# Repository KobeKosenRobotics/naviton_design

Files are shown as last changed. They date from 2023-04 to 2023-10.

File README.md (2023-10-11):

# naviton_design
[Naviton](https://github.com/KobeKosenRobotics/naviton)'s cad data and electric circuits



## Supporting format
### [Hardware design](https://github.com/KobeKosenRobotics/naviton_design/tree/main/hardware_design)
* Autodesk Inventor (.iam .ipt)
* Step file (.stp)
### [Electric design](https://github.com/KobeKosenRobotics/naviton_design/tree/main/electric_design)
* Autodesk Eagle(.brd .sch)

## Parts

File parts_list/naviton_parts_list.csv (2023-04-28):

カテゴリ | iam | メモ、備考 | 優先度 | 商社 | メーカー | メーカー型番 | 商社品名 | 注文コード | 数量 | 単価 | 小計
機械 | 機体 |  |  |  | amazon |  | ステンレス蝶番 ドアヒンジ 4‘’x3‘’ 厚さ3mm平蝶番 折り畳みヒンジ ドア用金物 家具補修 ステンレス鋼ねじ付き シルバー （2個セット ） | https://www.amazon.co.jp/%E3%82%B9%E3%83%86%E3%83%B3%E3%83%AC%E3%82%B9%E8%9D%B6%E7%95%AA-4%E2%80%98%E2%80%99x3%E2%80%98%E2%80%99-%E5%8E%9A%E3%81%953mm%E5%B9%B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 | 1
機械 | 機体 |  |  |  | amazon | 銅カットワイヤと100均箱で代用 | アスベル 保存容器 「Agタイトロック」 TLO-20 ナチュラル | https://www.amazon.co.jp/%E3%82%A2%E3%82%B9%E3%83%99%E3%83%AB-%E4%BF%9D%E5%AD%98%E5%AE%B9%E5%99%A8-%E3%80%8CAg%E3%82%BF%E3%82%A4%E3%83%88%E3%83%AD%E3%83%83%E3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 | 2
機械 | 機体 |  |  |  | amazon | 60Kg二軸サーボ 教育娯楽ロボットサーボ スマートロボットサーボ (180°) | 60Kg二軸サーボ 教育娯楽ロボットサーボ スマートロボットサーボ (180°) | https://www.amazon.co.jp/%E3%82%BE%E3%83%BC%E3%82%B9%E3%82%AB%E3%82%A4-60Kg%E4%BA%8C%E8%BB%B8%E3%82%B5%E3%83%BC%E3%83%9C-%E6%95%99%E8%82%B2%E5%A8%AF%E6%A5%BD%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 | 2
機械 | フレーム |  |  | 1 | misumi | HFS5-2020-800 | 高剛性フレーム | https://jp.misumi-ec.com/vona2/detail/110302683830/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 | 4
機械 | フレーム |  |  | 1 | misumi | HFS5-2020-300 | 高剛性フレーム | https://jp.misumi-ec.com/vona2/detail/110302683830/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 | 2
機械 | フレーム |  |  | 1 | misumi | HFS5-2020-716 | 高剛性フレーム | https://jp.misumi-ec.com/vona2/detail/110302683830/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 | 2
機械 | フレーム |  |  | 1 | misumi | HFS5-2020-500 | 高剛性フレーム | https://jp.misumi-ec.com/vona2/detail/110302683830/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 | 2
機械 | フレーム |  |  | 1 | misumi | HFS5-2020-600 | 高剛性フレーム | https://jp.misumi-ec.com/vona2/detail/110302683830/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 | 2
機械 | フレーム |  |  | 1 | misumi | HFS5-2020-400 | 高剛性フレーム | https://jp.misumi-ec.com/vona2/detail/110302683830/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 | 10
機械 | フレーム |  |  | 1 | misumi | HBLFSN5-SEP | ブラケット2 | https://jp.misumi-ec.com/vona2/detail/110300437260/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 | 54
機械 | フレーム |  |  | 1 | misumi | HFS5-2020-230 | 高剛性フレーム | https://jp.misumi-ec.com/vona2/detail/110302683830/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 | 2
機械 | フレーム |  |  | 1 | misumi | HFS5-2020-150 | 高剛性フレーム | https://jp.misumi-ec.com/vona2/detail/110302683830/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 | 2
機械 | 車軸部分 |  |  | 1 | misumi | SSFRHP12-140-F10-P8 | 車軸 | https://jp.misumi-ec.com/vona2/detail/110300088140/?HissuCode=SSFRHP12-140-F10-P8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 | 2
機械 | 車軸部分 |  |  | 1 | misumi | 自作or外注 カーボン化検討 | 車輪ハブ1 |  | 2
機械 | 車軸部分 |  |  | 1 | misumi | C-SFL6901ZZ | ベアリング12x18 | https://jp.misumi-ec.com/vona2/detail/110302554510/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 | 4
機械 | 車軸部分 |  |  | 1 | misumi | MJT-30C-RD-8-12 | カップリング | https://jp.misumi-ec.com/vona2/detail/221000131358/?KWSearch=MJT-30&searchFlow=results2products | 2
機械 | 車軸部分 |  |  | 1 | misumi | SCS12-12 | セットカラー | https://jp.misumi-ec.com/vona2/detail/110302636410/ | 4
機械 | 車軸部分 |  |  | 1 | misumi | 外注 | 車軸受け板3 | https://drive.google.com/file/d/1rCQuDQpkBceSkfm0FtveReuvyQ9fZlK2/view?usp=sharing | 4
機械 | 車軸部分 |  |  | 1 | misumi | SAPL-A-12X26 | メカロック | https://jp.misumi-ec.com/vona2/detail/221005492544/ | 2
機械 | 機体 |  |  | 1 | misumi | 477 | クッション | https://jp.misumi-ec.com/vona2/detail/223006733714/?searchFlow=results2products&list=PageSearchResult | 8
機械 |  |  |  | 1 | misumi | 外注 材質(SPCC(SPHC))表面処理(塗装(近似マンセル値2.5Y8/14)) | 緊急停止スイッチマウント |  | 2
機械 | 機体 |  |  |  | misumi | 外注(PET(スタンダード・透明)) | 防水1 |  | 2
機械 | 機体 |  |  |  | misumi | 外注(PET(スタンダード・透明)) | 防水2 |  | 1
機械 | 機体 |  |  |  | misumi | 外注(PET(スタンダード・透明)) | 防水4 |  | 1
機械 | 機体 |  |  |  | misumi | 外注(PET(スタンダード・透明)) | 防水3 |  | 1
機械 | 自由輪 |  |  | 3 | monotaro | ナンシン プレート式 自在、ゴム(B入り)車 車輪径D 150Φmm、許容荷重 160daN、STC-150CBC | 自由輪 | https://www.monotaro.com/p/3519/5946/ | 1
機械 | 車軸部分 |  |  | 1 | yahoo | モンキー・ゴリラ用 ８インチ アルミホイール・タイヤセット（ホイール選択：2.5J，タイヤ選択：90/65-8，オプション：組付けなし） | 車輪 | https://store.shopping.yahoo.co.jp/redmotoparts/ca085.html | 2
機械 | 車軸部分 |  |  | 1 | yahoo | 朱雀技研工房 | 小型DCギヤードモータ RS-775GM144-METAL-D Dカット軸・初段金属ギヤ仕様 | https://store.shopping.yahoo.co.jp/suzakulab/rs-775gm144-metal-d.html | 2
機械 | 車軸部分 |  |  |  | yahoo | 朱雀技研工房 | RS-775 1/144 接着剤601 | https://store.shopping.yahoo.co.jp/suzakulab/rs-775gm144-metal-r.html?sc_i=shp_pc_search_itemlist_shsrg_title | 2
機械 | 自由輪 | 外注 |  |  | ニワカソフト | 自由輪治具（t=3mm，d=180mm，w=100mm） | 自由輪マウント |  | 1
機械 | 車軸部分 | 外注 |  |  | ニワカソフト | 外注 カーボン化(t5) | 車軸受け板 |  | 4
機械 | 車軸部分 | 外注 |  |  | ニワカソフト | 外注 カーボン化(t3) | 車軸受け板2 |  | 2
機械 | 機体 | 外注 |  |  | ニワカソフト | 外注 カーボン化(t3) | LRFマウント |  | 2
機械 | 機体 | 教員対応 |  |  | 北陽電機 | UST-30LX | LiDAR |  | 2
機械 | 車軸部分 |  |  |  |  | 3Dプリンタ | モータースペーサ2 |  | 2
機械 | 車軸部分 |  |  |  |  | 3Dプリンタ | モータースペーサ |  | 2
機械 | 車軸部分 |  |  |  |  | 3Dプリンタ | エンコーダガード2 |  | 2
機械 | 機体 | 自作 |  |  |  |  | 回路スペース |  | 1
機械 | 機体 | 自作 |  |  |  |  | 回路スペース2 |  | 1
機械 | 機体 | 自作 |  |  |  |  | タイヤカバー |  | 2
電気部品 | 車軸部分 |  |  | 1 | Marutsu | AMT102-V | AMT102-1 | https://www.marutsu.co.jp/pc/i/1320459/ | 2
電気部品 |  | LANハブ |  | 1 | amazon |  | BUFFALO Giga対応 プラスチック筐体 AC電源 5ポート LSW6-GT-5EPL/NBK ブラック スイッチングハブ ローコストモデル 簡易パッケージ 壁掛け設置対応 日本メーカー | https://www.amazon.co.jp/%E3%83%97%E3%83%A9%E3%82%B9%E3%83%81%E3%83%83%E3%82%AF%E7%AD%90%E4%BD%93-LSW6-GT-5EPL-NBK-%E3%82%B9%E3%82%A4%E3%83%83%E3%83%81%E3%83%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 | 1 | 1280 | 1280
電気部品 |  | usbハブ |  | 1 | amazon |  | Anker USB3.0 ウルトラスリム 4ポートハブ, USB ハブ バスパワー 軽量 コンパクト MacBook / iMac / Surface Pro 等 ノートPC 他対応 USBハブ テレワーク リモート 在宅勤務 | https://www.amazon.co.jp/Anker-USB3-0-%E3%82%A6%E3%83%AB%E3%83%88%E3%83%A9%E3%82%B9%E3%83%AA%E3%83%A0-4%E3%83%9D%E3%83%BC%E3%83%88%E3%83%8F%E3%83%96-%E3%80%90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 | 1 | 1399 | 1399
電気部品 |  | usb延長 |  | 1 | amazon | 右L型 | 変換名人 USB3.0 延長ケーブル 20cm [ Aオス端子・、右L型 ] USB3A-CA20RL | https://www.amazon.co.jp/%E5%A4%89%E6%8F%9B%E5%90%8D%E4%BA%BA-USB3-0-%E5%BB%B6%E9%95%B7%E3%82%B1%E3%83%BC%E3%83%96%E3%83%AB-A%E3%82%AA%E3%82%B9%E7%AB%AF%E5%AD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 | 1 | 575 | 575
電気部品 |  | btドングル |  | 1 | amazon |  | BUFFALO Bluetooth4.0 Class1対応 USBアダプター BSBT4D105BK | https://www.amazon.co.jp/BUFFALO-Bluetooth4-0-Class1%E5%AF%BE%E5%BF%9C-USB%E3%82%A2%E3%83%80%E3%83%97%E3%82%BF%E3%83%BC-BSBT4D105BK/dp/B07716SP6N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 | 1 | 2299 | 2299
電気部品 |  | コントローラ |  | 1 | amazon |  | ワイヤレスコントローラー (DUALSHOCK 4) マグマ・レッド (CUH-ZCT2J11) | https://www.amazon.co.jp/%E3%83%AF%E3%82%A4%E3%83%A4%E3%83%AC%E3%82%B9%E3%82%B3%E3%83%B3%E3%83%88%E3%83%AD%E3%83%BC%E3%83%A9%E3%83%BC-DUALSHOCK-4-%E3%83%9E%E3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 | 1 | 6480 | 6480
電気部品 |  | pro mini |  | 1 | amazon |  | HiLetgo ATMEGA328P 3.3V/8M Arduino PROミニ 互換性のある開発ボード改良版 (3.3V) (2個セット) | https://www.amazon.co.jp/HiLetgo-ATMEGA328P-Arduino-PRO%E3%83%9F%E3%83%8B-%E4%BA%92%E6%8F%9B%E6%80%A7%E3%81%AE%E3%81%82%E3%82%8B%E9%96%8B%E7%99%BA%E3%83%9C%E3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 | 1 | 1030 | 1030
電気部品 |  | mini usb host |  | 1 | amazon |  | GAOHOU ミニUSBホストシールド2.0 ADK SLR開発ツール互換SPIインターフェイス | https://www.amazon.co.jp/GAOHOU-BU0295-%E3%83%9F%E3%83%8BUSB%E3%83%9B%E3%82%B9%E3%83%88%E3%82%B7%E3%83%BC%E3%83%AB%E3%83%892-0-ADK-SLR%E9%96%8B%E7%99%BA%E3%83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 | 1 | 998 | 998
電気部品 |  | 緊急停止スイッチ |  | 1 | misumi | AR30V0R-11R | φ30 非常停止用押しボタンスイッチ AR30形 (AR30V0R-11R) | https://jp.misumi-ec.com/vona2/detail/222000260284/?HissuCode=AR30V0R-11R | 2 | 1289 | 2578
電気部品 |  | モータドライバ |  | 1 | yahoo | 朱雀技研工房 | Cytron 30A 5V-30V DCモータドライバ | https://store.shopping.yahoo.co.jp/suzakulab/cytron-md30c.html# | 2 | 3947 | 7894
電気部品 |  | teensy3.6 |  | 1 | スイッチサイエンス |  | Teensy 3.6 | https://www.switch-science.com/catalog/2989/ | 1 | 4533 | 4533
電気部品 |  | imu |  | 1 | スイッチサイエンス |  | Adafruit BNO055搭載 9DoF 方位/慣性計測モジュール | https://www.switch-science.com/catalog/5511/ | 1 | 5489 | 5489
電気部品 |  | スイッチング電源 |  | 1 | 秋月電子 |  | 最大２Ａ ３～１６Ｖ降圧型スイッチングモジュールキット（ＭＰＭ８０使用） | https://akizukidenshi.com/catalog/g/gK-08572/ | 2 | 750 | 1500

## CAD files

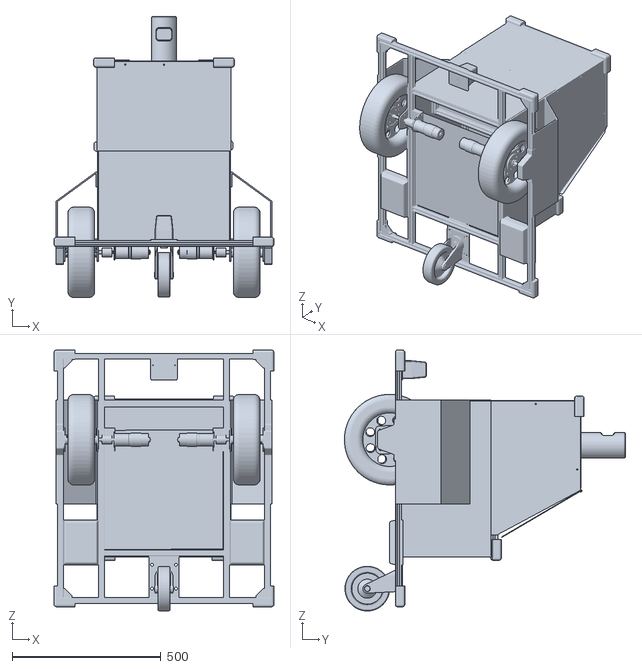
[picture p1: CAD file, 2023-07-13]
hardware_design/naviton.stl
738.0 x 943.7 x 876.0

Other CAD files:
hardware_design/step/機体.stp
hardware_design/inventor/AMT102 outside.ipt
hardware_design/inventor/AMT102-1.ipt
hardware_design/inventor/IG42C-144.ipt
hardware_design/inventor/LRFマウント.ipt
hardware_design/inventor/PCパーツ1.ipt
hardware_design/inventor/PCパーツ2.ipt
hardware_design/inventor/RS-775.ipt
hardware_design/inventor/RS-775GM.ipt
hardware_design/inventor/hdl32e.ipt
hardware_design/inventor/moldspace.iam
hardware_design/inventor/pixy.ipt
hardware_design/inventor/pixymount1.ipt
hardware_design/inventor/pixymount2.ipt
hardware_design/inventor/pixyユニット.iam
hardware_design/inventor/raida- .ipt
hardware_design/inventor/おもり.ipt
hardware_design/inventor/くさび.ipt
hardware_design/inventor/エンコーダガード.ipt
hardware_design/inventor/エンコーダガード2.ipt
hardware_design/inventor/カップリング.ipt
hardware_design/inventor/カメラマウント.ipt
hardware_design/inventor/ガイド輪.ipt
hardware_design/inventor/ガイド輪マウント.ipt
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

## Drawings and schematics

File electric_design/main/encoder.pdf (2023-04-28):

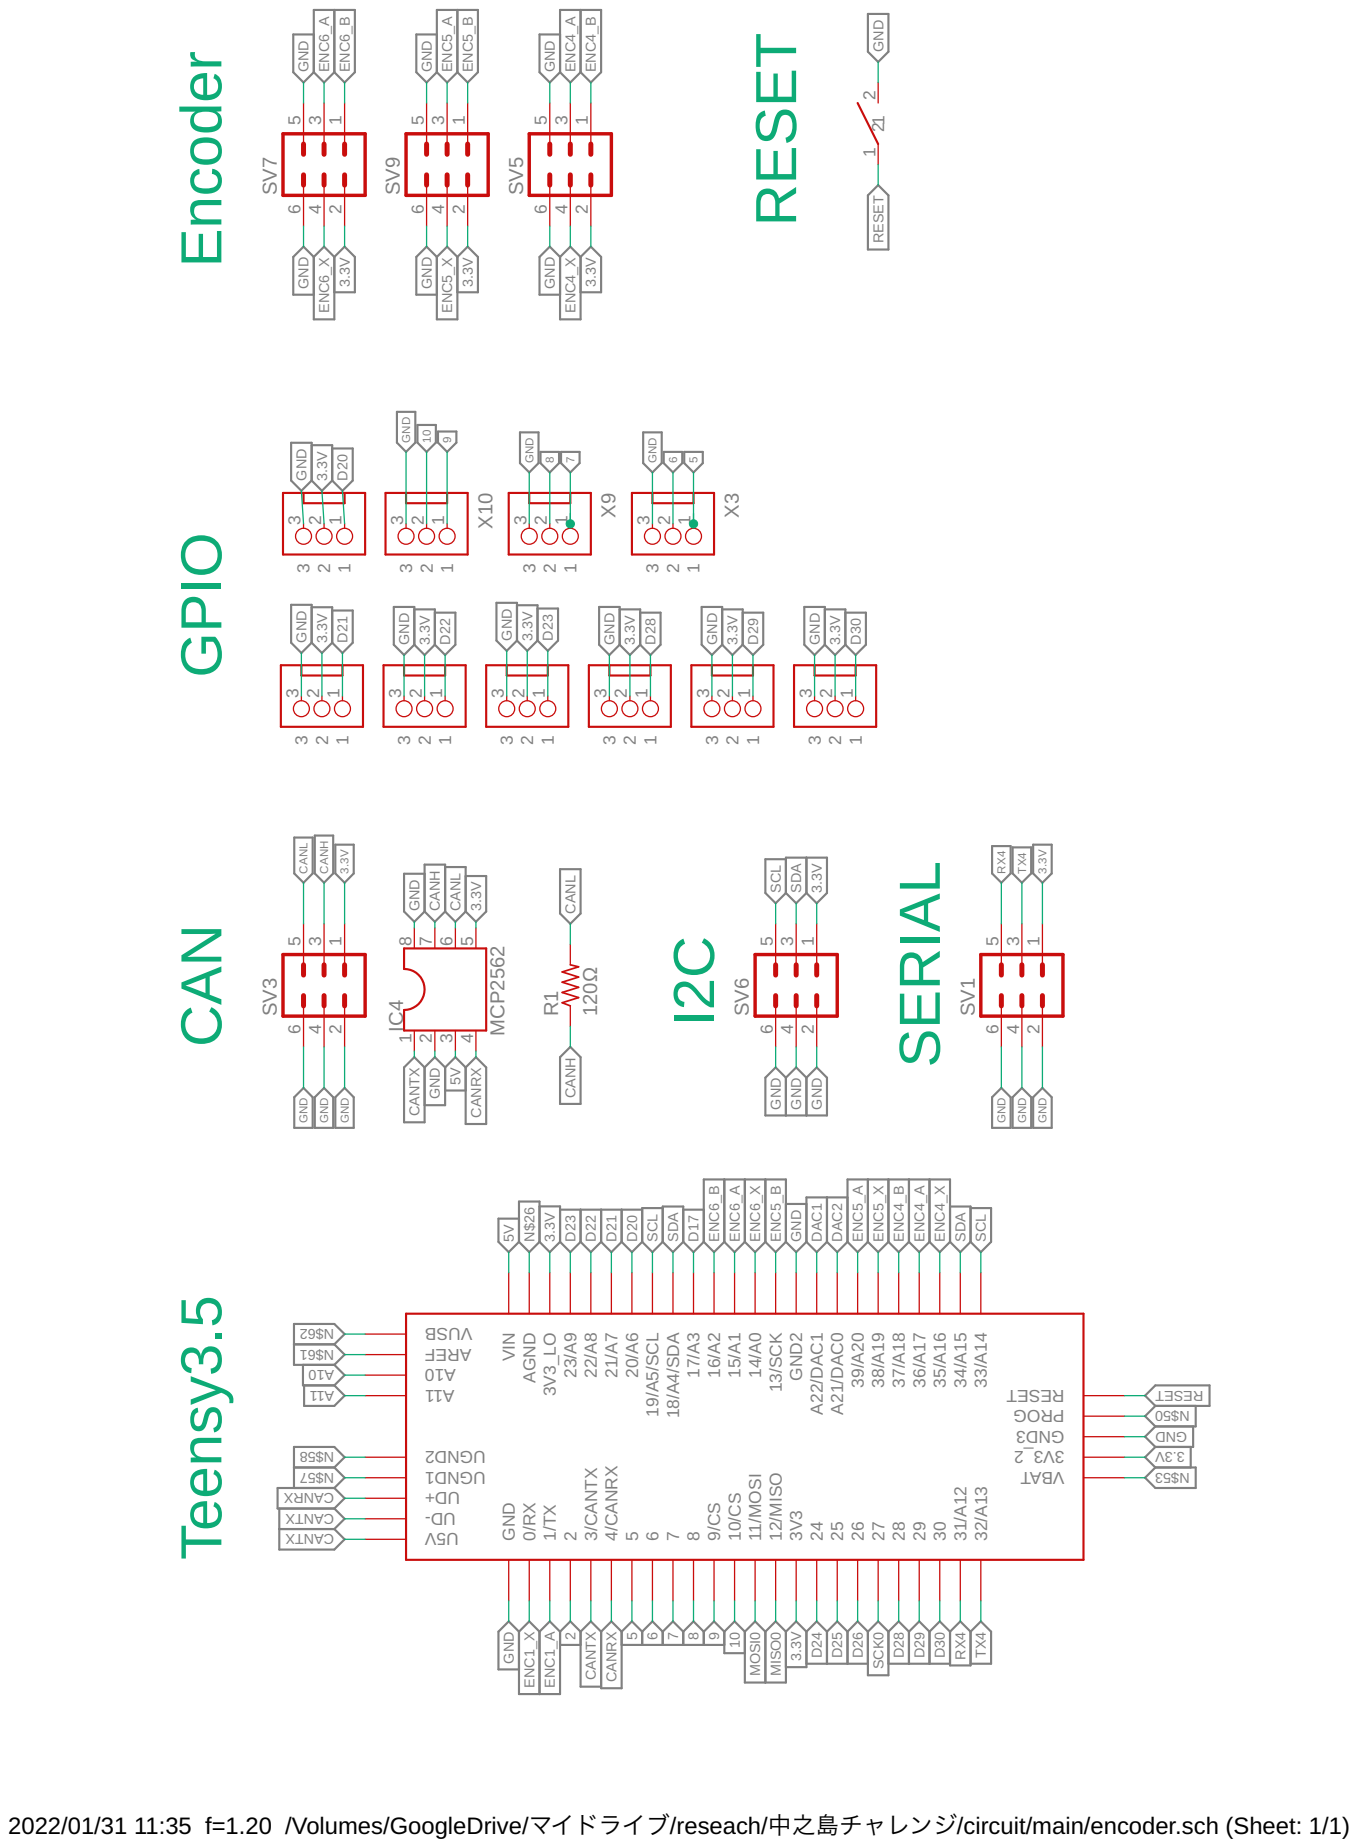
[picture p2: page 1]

GND GND GND GND GND GND GND

2022/01/31 11:35 f=1.20 /Volumes/GoogleDrive/マイドライブ/reseach/中之島チャレンジ/circuit/main/encoder.sch (Sheet: 1/1)

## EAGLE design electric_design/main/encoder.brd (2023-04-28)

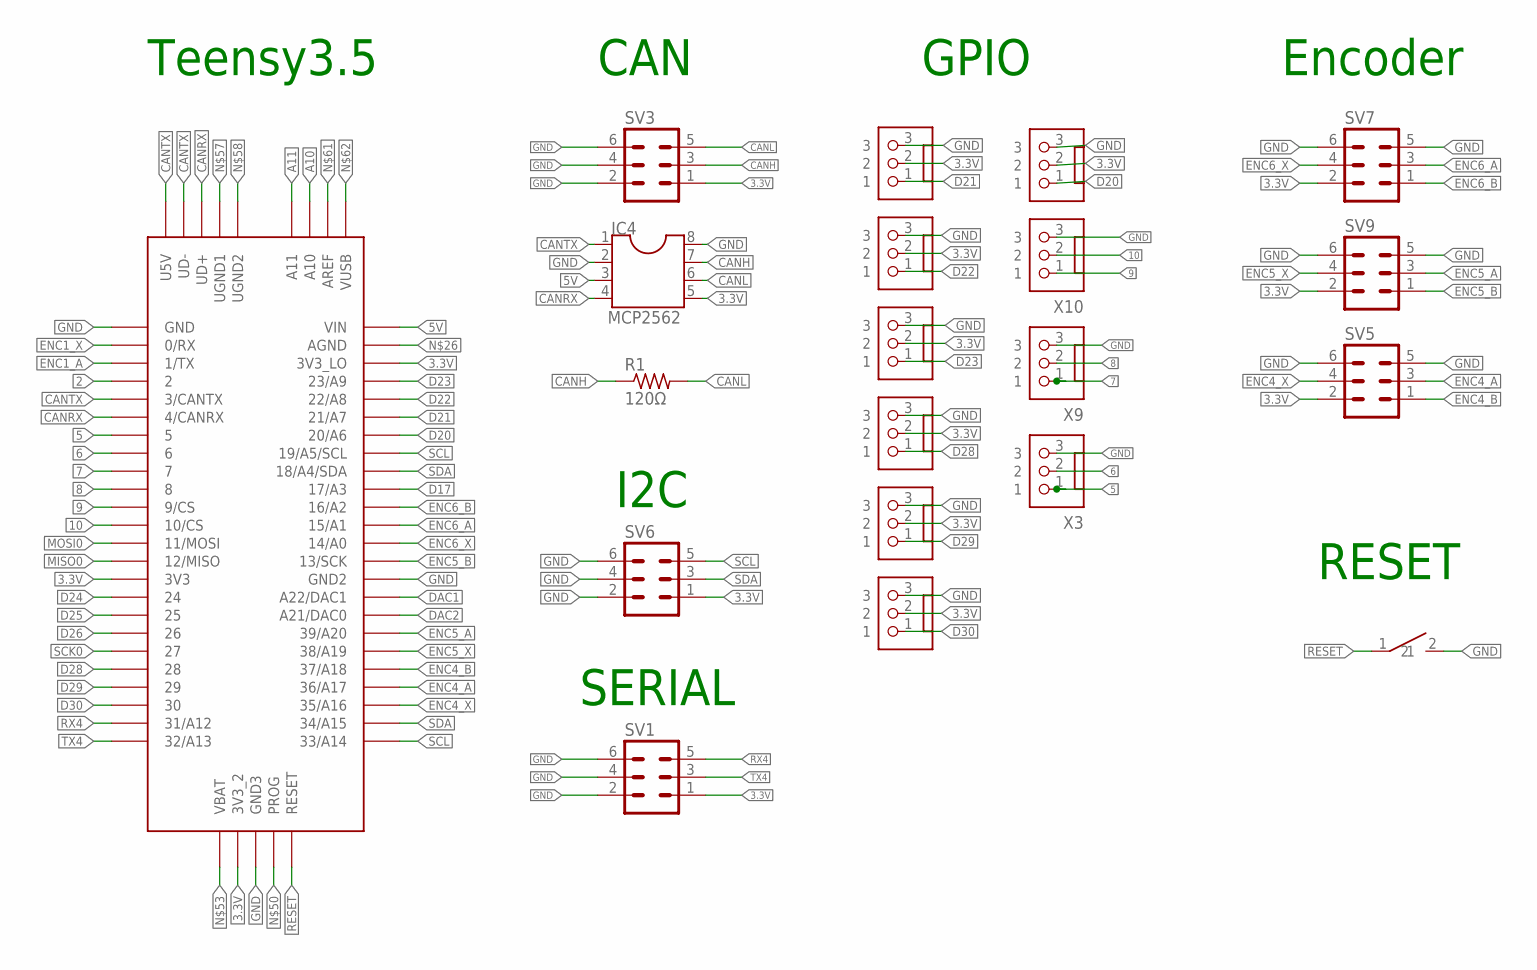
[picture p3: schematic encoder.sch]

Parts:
IC4: MCP2562; DIL08
R1: 120Ω; 0207/7
SV1, SV3, SV5, SV6, SV7, SV9: ML6
TACT_SWITCH1: TACT_SWITCH
U$1: TEENSY_3.5/3.6
X3, X6, X7, X8, X9, X10, X12, X13, X14, X15: JST-XH-03-PIN-LONG-PAD; JST-XH-03-PACKAGE-LONG-PAD

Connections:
2: U$1.2
3.3V: IC4.5, SV1.1, SV3.1, SV5.2, SV6.1, SV7.2, SV9.2, U$1.3V3, U$1.3V3_2, U$1.3V3_LO, X6.2, X7.2, X8.2, X12.2, X13.2, X14.2, X15.2
5: U$1.5, X3.1
5V: IC4.3, U$1.VIN
6: U$1.6, X3.2
7: U$1.7, X9.1
8: U$1.8, X9.2
9: U$1.9/CS, X10.1
10: U$1.10/CS, X10.2
A10: U$1.A10
A11: U$1.A11
CANH: IC4.7, R1.1, SV3.3
CANL: IC4.6, R1.2, SV3.5
CANRX: IC4.4, U$1.4/CANRX, U$1.UD+
CANTX: IC4.1, U$1.3/CANTX, U$1.U5V, U$1.UD-
D17: U$1.17/A3
D20: U$1.20/A6, X6.1
D21: U$1.21/A7, X7.1
D22: U$1.22/A8, X12.1
D23: U$1.23/A9, X13.1
D24: U$1.24
D25: U$1.25
D26: U$1.26
D28: U$1.28, X8.1
D29: U$1.29, X14.1
D30: U$1.30, X15.1
DAC1: U$1.A22/DAC1
DAC2: U$1.21/DAC0 (A21/DAC0)
ENC1_A: U$1.1/TX
ENC1_X: U$1.0/RX
ENC4_A: SV5.3, U$1.36/A17
ENC4_B: SV5.1, U$1.37/A18
ENC4_X: SV5.4, U$1.35/A16
ENC5_A: SV9.3, U$1.39/A20
ENC5_B: SV9.1, U$1.13/SCK
ENC5_X: SV9.4, U$1.38/A19
ENC6_A: SV7.3, U$1.15/A1
ENC6_B: SV7.1, U$1.16/A2
ENC6_X: SV7.4, U$1.14/A0
GND: IC4.2, IC4.8, SV1.2, SV1.4, SV1.6, SV3.2, SV3.4, SV3.6, SV5.5, SV5.6, SV6.2, SV6.4, SV6.6, SV7.5, SV7.6, SV9.5, SV9.6, TACT_SWITCH1.2, U$1.GND, U$1.GND2, U$1.GND3, X3.3, X6.3, X7.3, X8.3, X9.3, X10.3, X12.3, X13.3, X14.3, X15.3
MISO0: U$1.12/MISO
MOSI0: U$1.11/MOSI
RESET: TACT_SWITCH1.1, U$1.RESET
RX4: SV1.5, U$1.31/A12
SCK0: U$1.27
SCL: SV6.5, U$1.19/A5/SCL, U$1.33/A14
SDA: SV6.3, U$1.18/A4/SDA, U$1.34/A15
TX4: SV1.3, U$1.32/A13

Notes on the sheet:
Teensy3.5
Encoder
I2C
SERIAL
GPIO
CAN
RESET

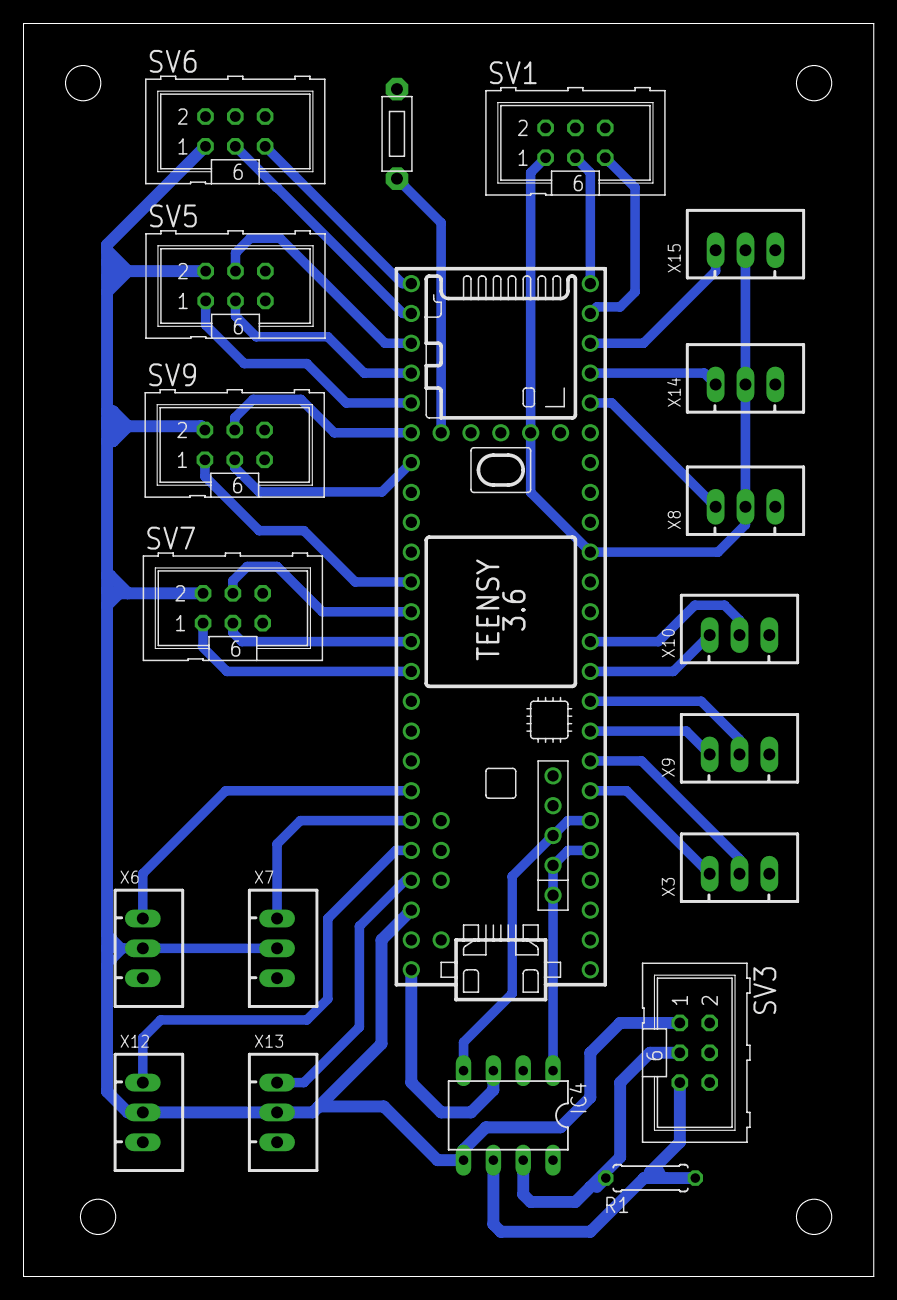
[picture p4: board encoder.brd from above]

Board: 2 copper layers, 72.4 x 106.7 mm, 20 parts (0 on the bottom side), 34 nets.

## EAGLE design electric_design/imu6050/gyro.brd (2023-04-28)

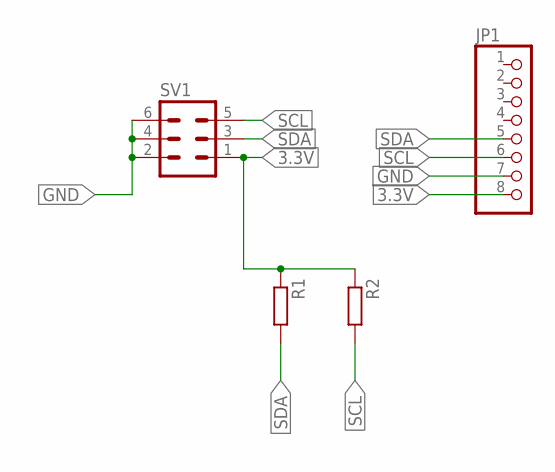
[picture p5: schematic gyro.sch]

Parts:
JP1: PINHD-1X8; 1X08
R1, R2: R-EU_0309/12; 0309/12
SV1: ML6

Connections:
3.3V: JP1.8, R1.1, R2.1, SV1.1
GND: JP1.7, SV1.2, SV1.4, SV1.6
SCL: JP1.6, R2.2, SV1.5
SDA: JP1.5, R1.2, SV1.3

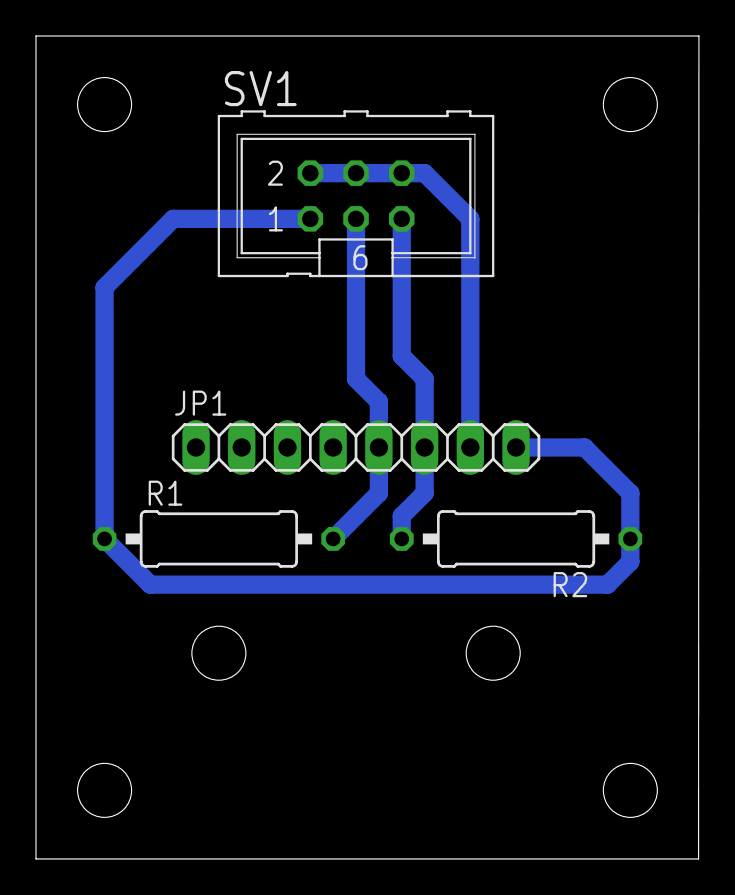
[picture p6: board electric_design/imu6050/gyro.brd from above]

Board: 2 copper layers, 36.8 x 45.7 mm, 4 parts (0 on the bottom side), 4 nets.

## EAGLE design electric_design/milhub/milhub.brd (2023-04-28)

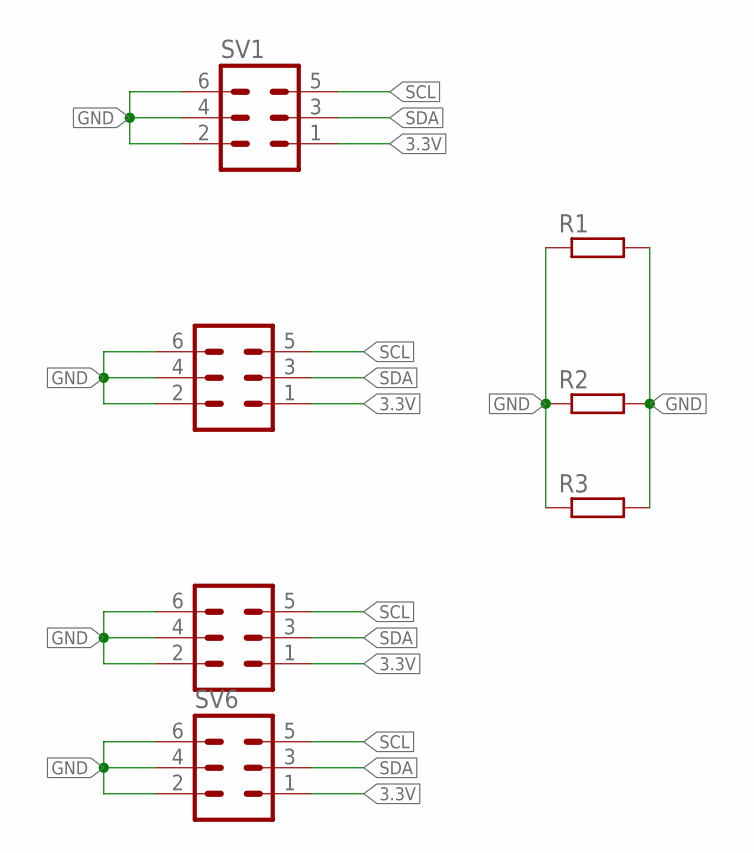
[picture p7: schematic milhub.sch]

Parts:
R1, R2, R3: R-EU_0207/10; 0207/10
SV1, SV3, SV5, SV6: ML6

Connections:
3.3V: SV1.1, SV3.1, SV5.1, SV6.1
GND: R1.1, R1.2, R2.1, R2.2, R3.1, R3.2, SV1.2, SV1.4, SV1.6, SV3.2, SV3.4, SV3.6, SV5.2, SV5.4, SV5.6, SV6.2, SV6.4, SV6.6
SCL: SV1.5, SV3.5, SV5.5, SV6.5
SDA: SV1.3, SV3.3, SV5.3, SV6.3

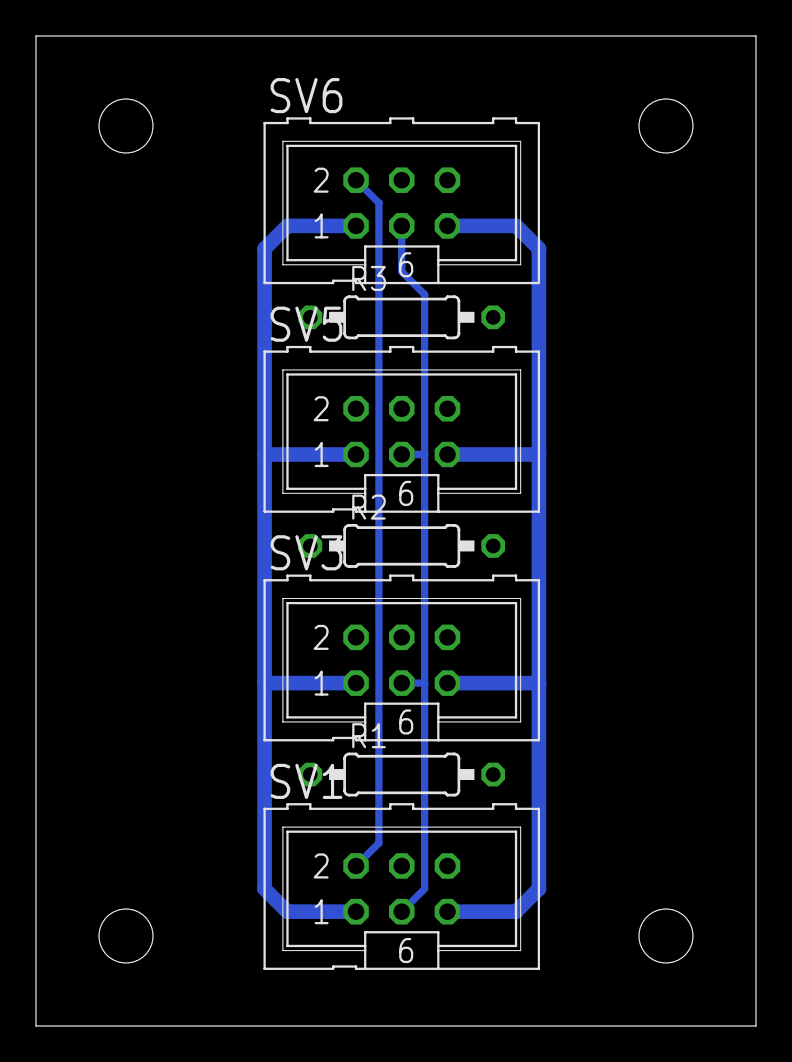
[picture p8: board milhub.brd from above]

Board: 2 copper layers, 40.0 x 55.0 mm, 7 parts (0 on the bottom side), 4 nets.

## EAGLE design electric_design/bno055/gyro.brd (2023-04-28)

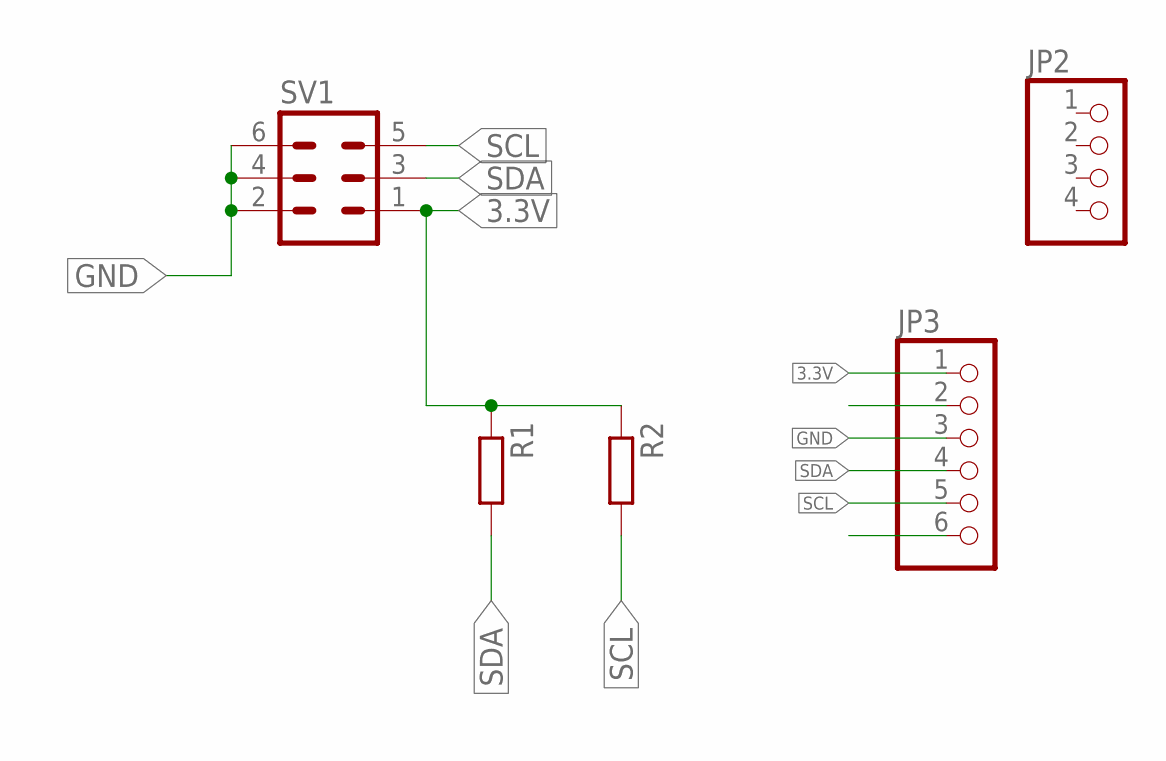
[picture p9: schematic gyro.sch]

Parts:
JP2: PINHD-1X4; 1X04
JP3: PINHD-1X6; 1X06
R1, R2: R-EU_0309/12; 0309/12
SV1: ML6

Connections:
3.3V: JP3.1, R1.1, R2.1, SV1.1
GND: JP3.3, SV1.2, SV1.4, SV1.6
SCL: JP3.5, R2.2, SV1.5
SDA: JP3.4, R1.2, SV1.3

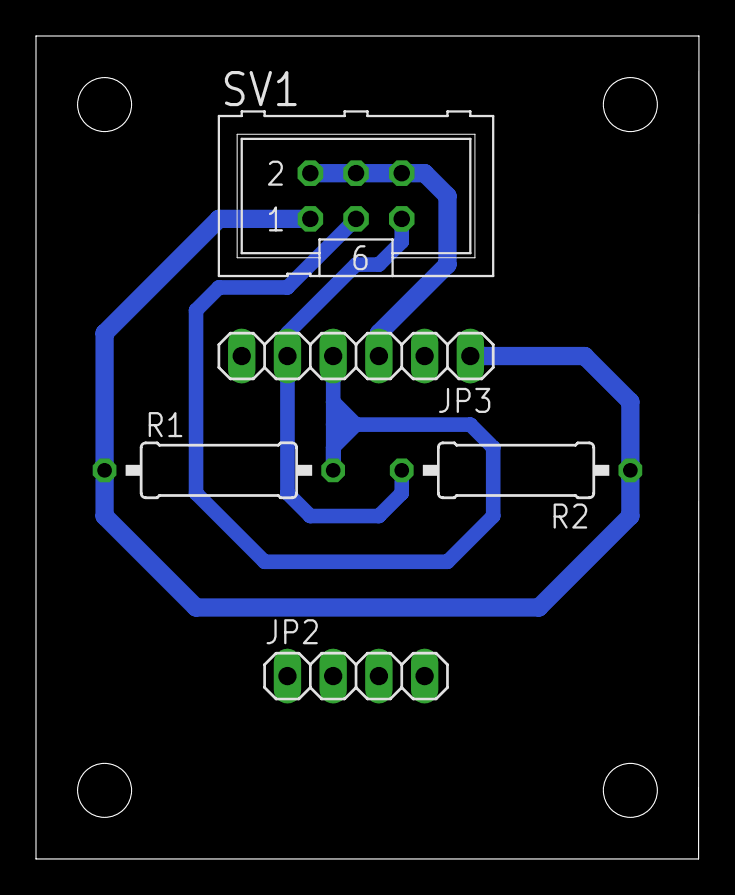
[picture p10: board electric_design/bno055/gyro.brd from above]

Board: 2 copper layers, 36.8 x 45.7 mm, 5 parts (0 on the bottom side), 4 nets.

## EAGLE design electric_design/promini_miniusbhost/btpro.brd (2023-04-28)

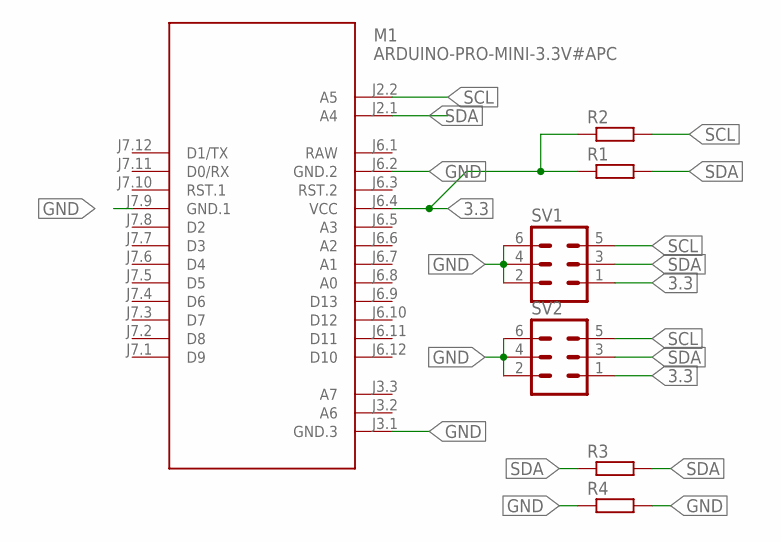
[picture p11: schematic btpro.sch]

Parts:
M1: ARDUINO-PRO-MINI-3.3V#APC; ARDUINO-PRO-MINI#APC
R1, R2: R-EU_0411/12; 0411/12
R3, R4: R-EU_0207/10; 0207/10
SV1, SV2: ML6

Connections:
3.3: M1.J6.4 (VCC), R1.1, R2.1, SV1.1, SV2.1
GND: M1.J3.1 (GND.3), M1.J6.2 (GND.2), M1.J7.9 (GND.1), R4.1, R4.2, SV1.2, SV1.4, SV1.6, SV2.2, SV2.4, SV2.6
RAW: M1.J6.1 (RAW)
SCL: M1.J2.2 (A5), R2.2, SV1.5, SV2.5
SDA: M1.J2.1 (A4), R1.2, R3.1, R3.2, SV1.3, SV2.3

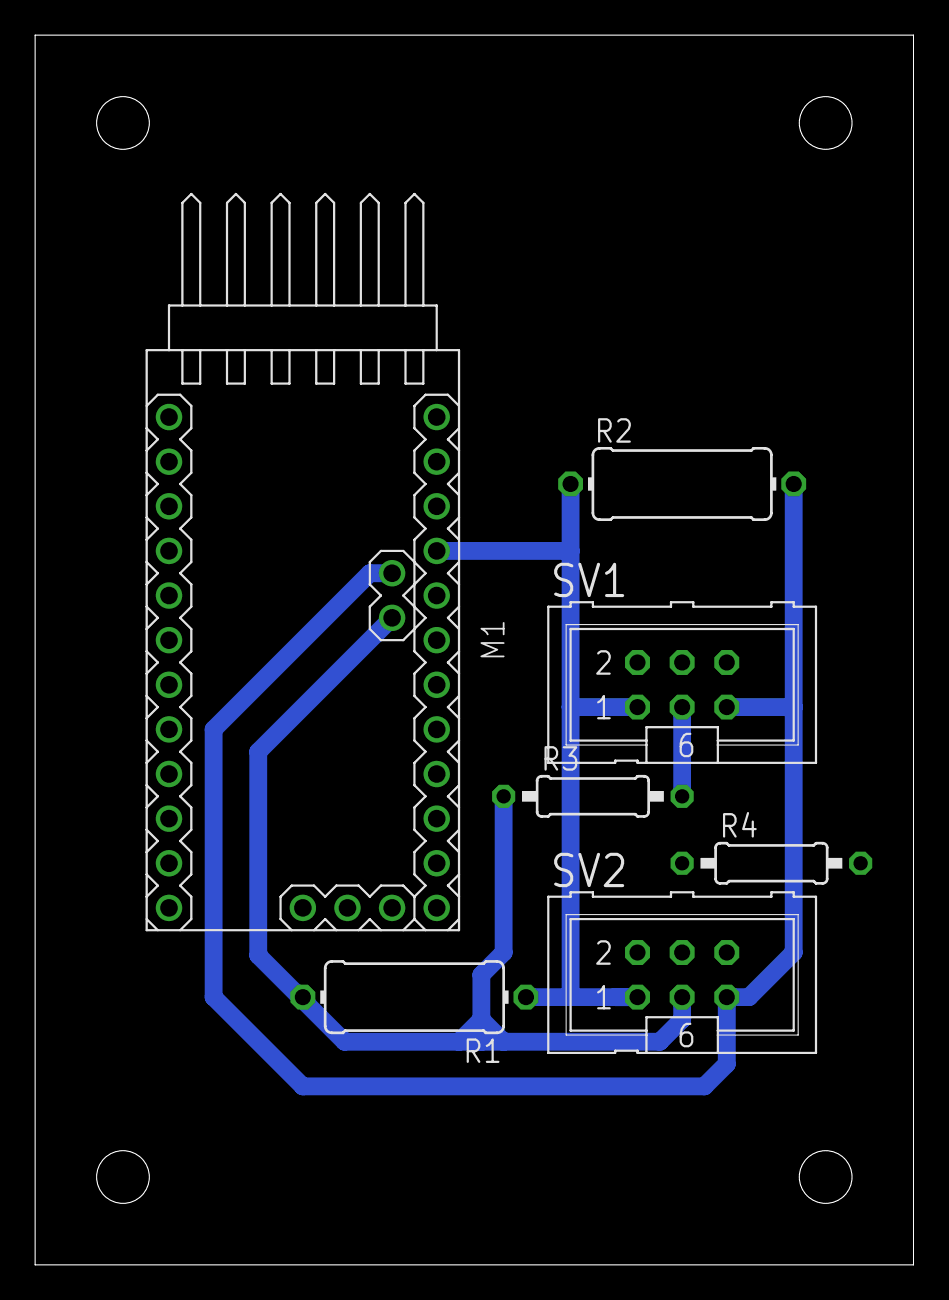
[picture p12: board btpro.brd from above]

Board: 2 copper layers, 50.0 x 70.0 mm, 7 parts (0 on the bottom side), 4 nets.

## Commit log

2023-04-28 upload circuit data
    [btpro.brd, btpro.sch, encoder.brd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]
2023-07-13 add cad data
    [AMT102 outside.ipt, AMT102-1.ipt, IG42C-144.ipt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]
2023-07-13 fix stl
    [機体.stp]

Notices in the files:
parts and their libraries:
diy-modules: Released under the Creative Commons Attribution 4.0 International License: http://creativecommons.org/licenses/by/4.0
